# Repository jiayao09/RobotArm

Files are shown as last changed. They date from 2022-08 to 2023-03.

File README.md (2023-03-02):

# RobotArm
This a robotic arm with a 4 DOF developed based on MeArm model for further development. Take a look at my BOM and assembly drawing PDF to build the same model.
(check out start.ino)


Figure 1:Robotic arm with Laser cutting update
</br>
</br>

https://user-images.githubusercontent.com/110358483/185725085-09091f4c-c75e-4899-8eab-52e4dab4b233.mp4

# list of file
- Detail BOM
- STL file for 3D printing
- Laser cutting file for gripper version 2 (optional)
- Assembly drawings for installation
- Code for the above video （Control Board：Arduino）

</br>

#  RECENT UPDATE:
I've recently decided to increase the arm's degrees of freedom from 4 to 6. This design demo builds upon the Niryo One concept by adding new elements. The detail drawing and bill of materials (BOM) is up-to-date. The new design expands on the original functionality by including new interfaces and hardware.



### Check out the development process here:  https://github.com/jiayao09/RobotArm/tree/6-DOF-Robot-Arm

</br>

# Included Functions:
### Control by coding

https://user-images.githubusercontent.com/110358483/185726008-0d00c303-87b9-40a1-b045-875e55abf965.mp4

### Control by phone with the HC-06 Bluetooth module (check out start.ino)

https://user-images.githubusercontent.com/110358483/185725174-6e9ee21b-cd90-49b7-b49f-77a15e82c952.mp4

</br>

### Control by Wearable-Controller
Check out more information here: https://github.com/jiayao09/Wearable_Controller.git
- Sensor and control board:
   - Arduino uno
   - Servo KN99 X 4
   - NRF24L01



</br>

### Control by ESP32 cam for image recognition (Pending)
- Add object or color detection
- Move to detect object position

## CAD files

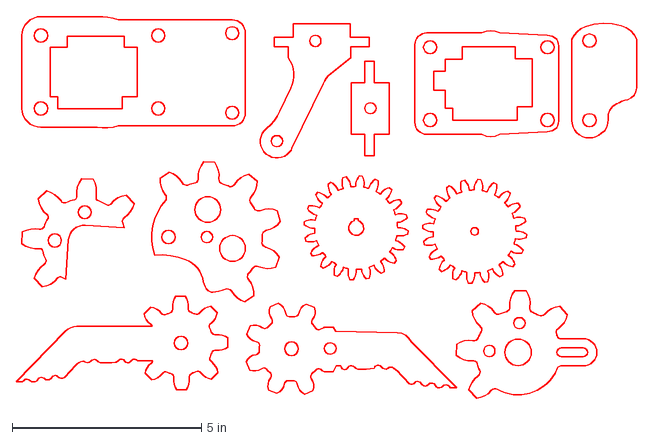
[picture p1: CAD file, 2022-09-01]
3mm.dxf
16.4 x 10.2 in

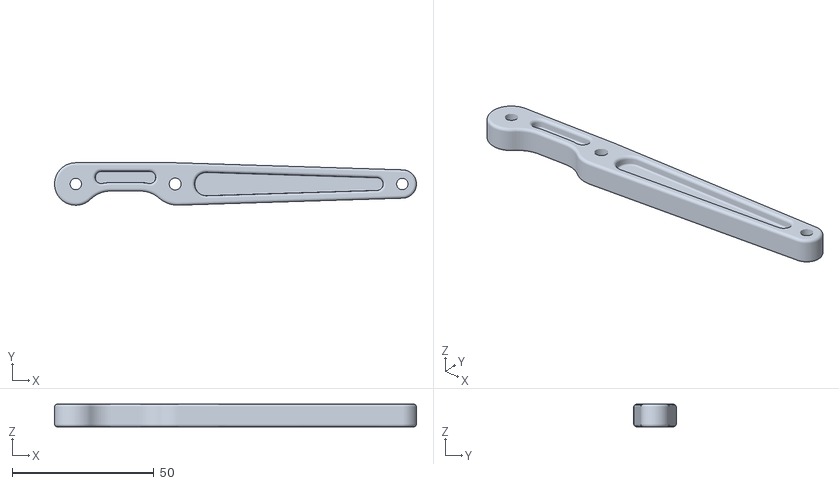
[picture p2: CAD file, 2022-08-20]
STL file/EBA_01.00.005_horizontal_arm.STL
127.5 x 15.0 x 8.00

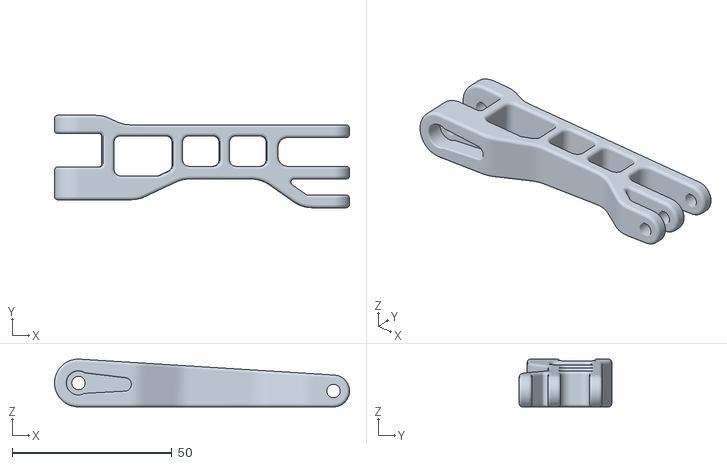
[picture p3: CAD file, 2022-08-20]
STL file/EBA_01.00.004_forward_drive_arm.STL
92.5 x 29.0 x 15.0

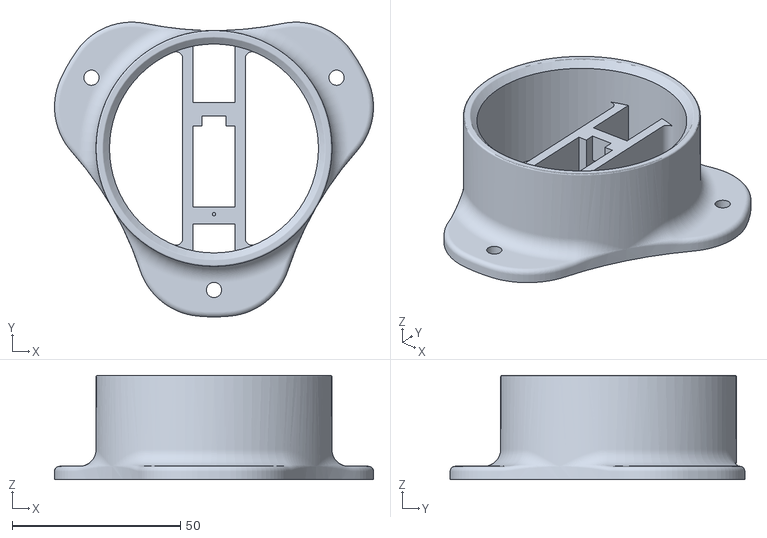
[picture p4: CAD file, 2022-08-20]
STL file/EBA_01.00.010_basement.STL
94.7 x 87.5 x 31.0

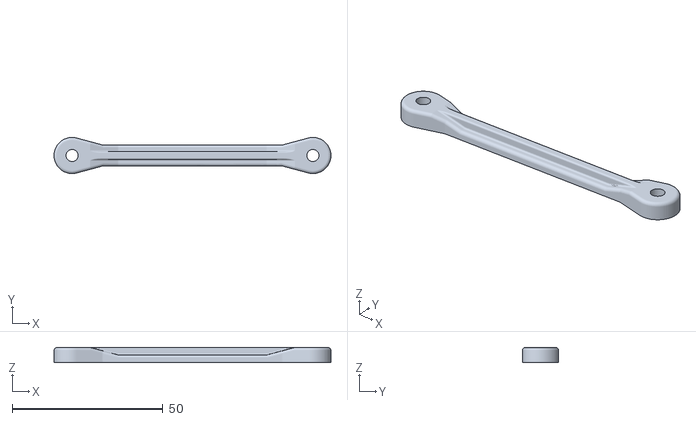
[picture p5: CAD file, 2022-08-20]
STL file/EBA_01.00.003_link.STL
92.0 x 12.0 x 5.00

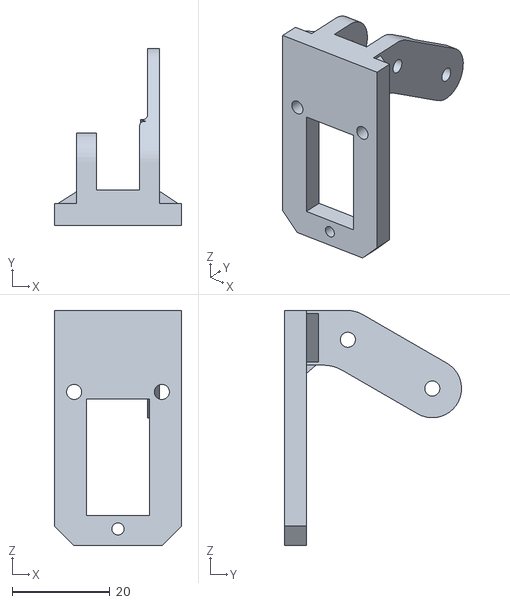
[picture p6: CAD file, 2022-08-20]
STL file/EBA_01.00.012_R01_claw_support_upgrade.STL
26.1 x 36.3 x 48.2

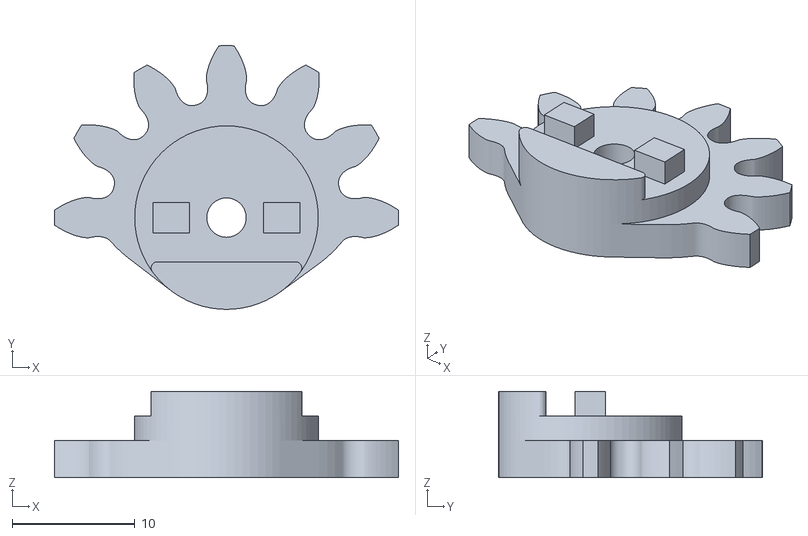
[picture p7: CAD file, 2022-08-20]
STL file/EBA_01.00.016_R01_driven_gear.STL
28.0 x 21.5 x 7.00

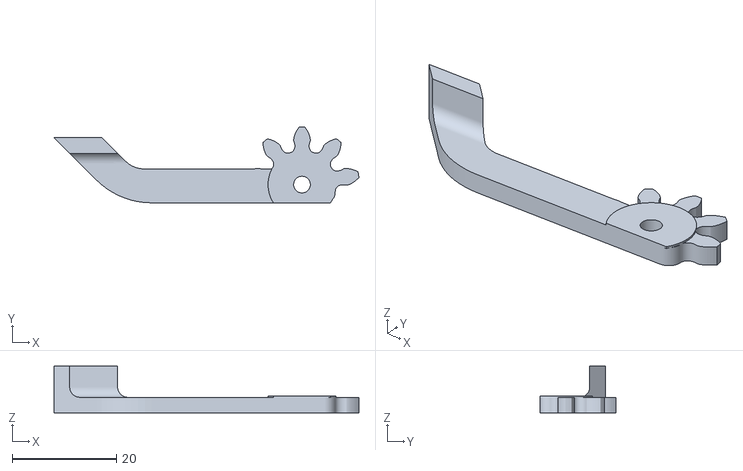
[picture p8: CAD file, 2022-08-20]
STL file/EBA_01.00.014_R01_left_finger.STL
58.4 x 14.5 x 9.00

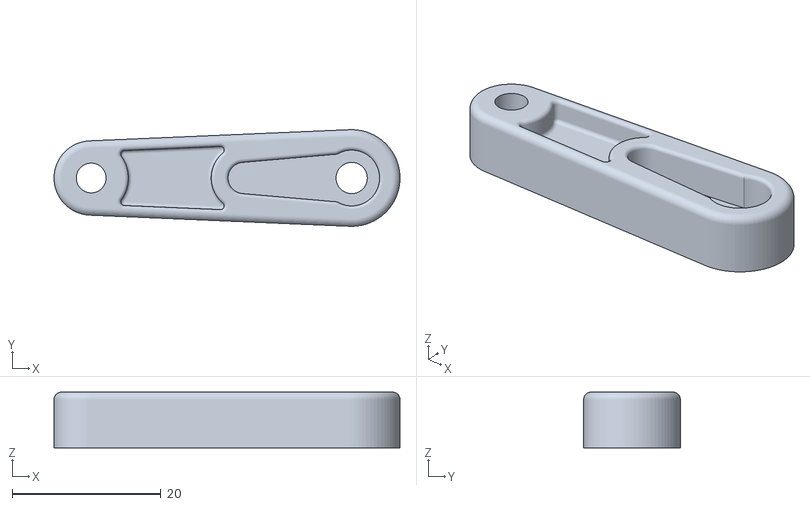
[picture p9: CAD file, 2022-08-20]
STL file/EBA_01.00.002_vertical_drive_arm.STL
46.5 x 13.0 x 7.50

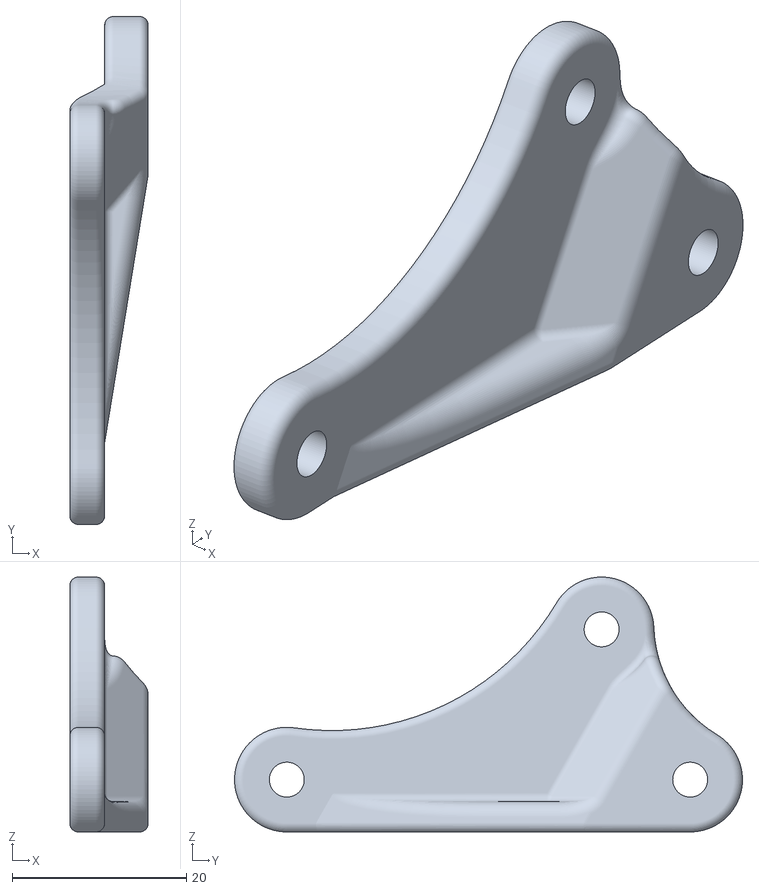
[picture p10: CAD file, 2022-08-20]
STL file/EBA_01.00.006_triangular_link.STL
9.00 x 58.3 x 29.2

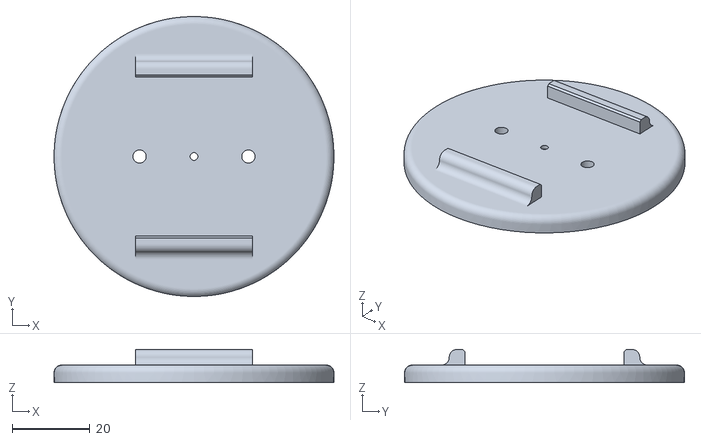
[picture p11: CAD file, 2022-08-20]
STL file/EBA_01.00.011_round_plate.STL
72.0 x 72.0 x 8.50

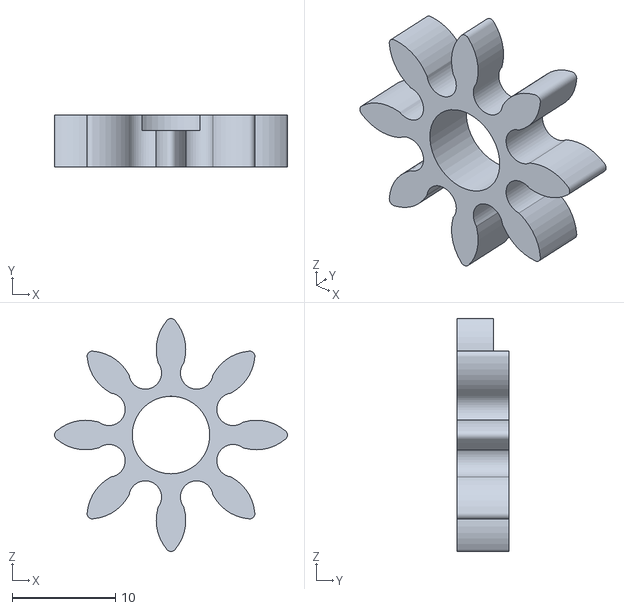
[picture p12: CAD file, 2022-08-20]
STL file/EBA_01.00.015_drive gear_upgrade.STL
22.5 x 5.00 x 22.5

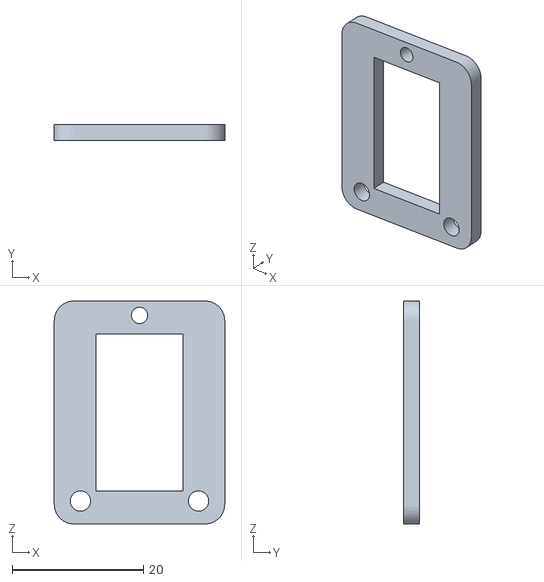
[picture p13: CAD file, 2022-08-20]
STL file/EBA_01.00.009_servo_plate_upgrade.STL
26.0 x 2.50 x 34.0

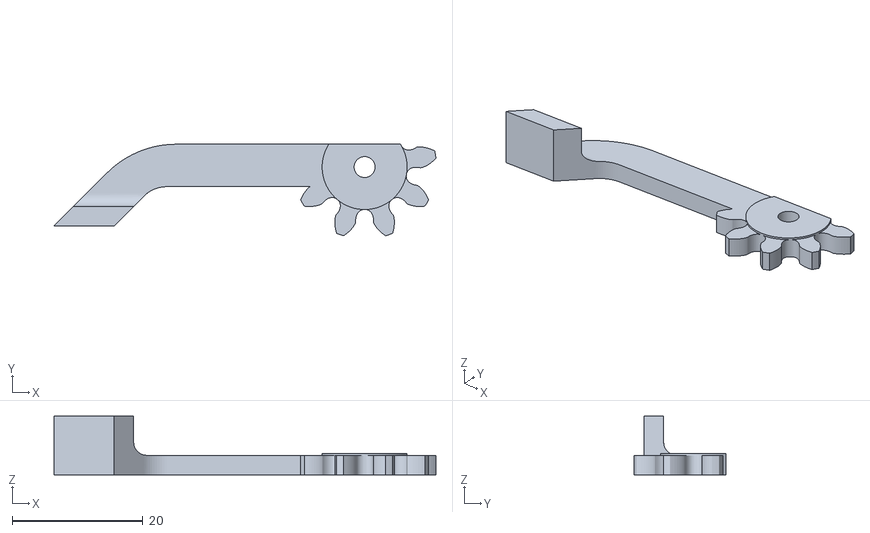
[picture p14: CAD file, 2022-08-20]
STL file/EBA_01.00.013_R01_right_finger.STL
58.4 x 14.0 x 9.00

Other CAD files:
STL file/EBA_01.00.001.STL

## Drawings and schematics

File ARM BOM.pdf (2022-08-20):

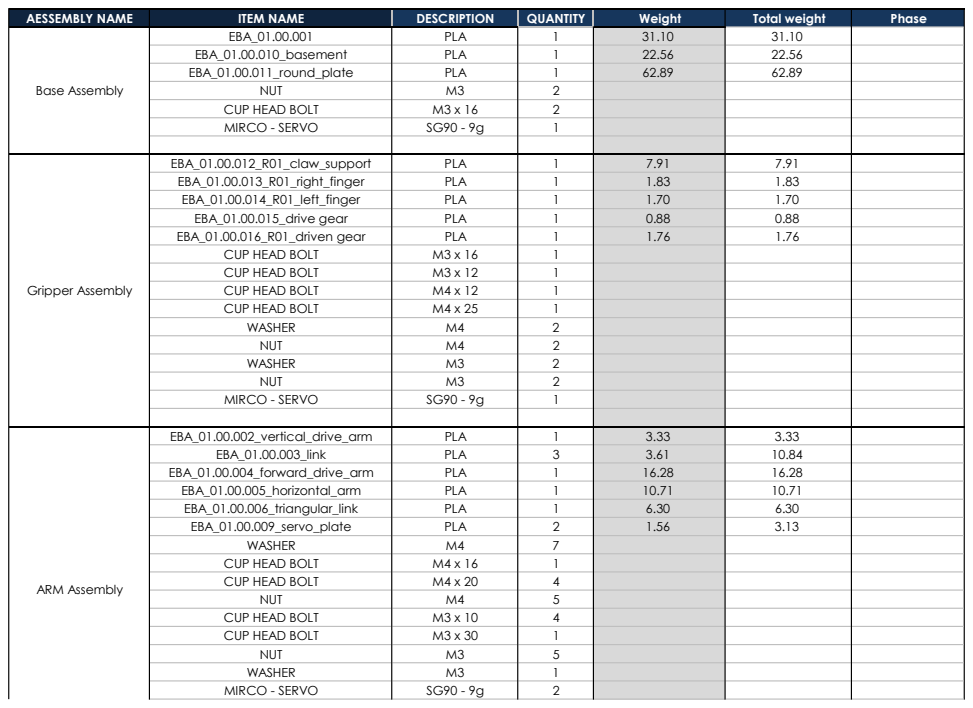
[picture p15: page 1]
EBA_01.00.012_R01_claw_support; PLA; EBA_01.00.013_R01_right_finger; EBA_01.00.014_R01_left_finger; EBA_01.00.015_drive gear; EBA_01.00.016_R01_driven gear; CUP HEAD BOLT; WASHER; NUT; MIRCO - SERVO; EBA_01.00.002_vertical_drive_arm; EBA_01.00.003_link; EBA_01.00.004_forward_drive_arm; EBA_01.00.005_horizontal_arm; EBA_01.00.006_triangular_link; EBA_01.00.009_servo_plate; Gripper Assembly; ARM Assembly

AESSEMBLY NAME | ITEM NAME | DESCRIPTION | QUANTITY | Weight | Total weight 31.10 22.56 62.89 | Phase
Base Assembly | EBA_01.00.001 EBA_01.00.010_basement EBA_01.00.011_round_plate NUT CUP HEAD BOLT MIRCO - SERVO | PLA PLA PLA M3 M3 x 16 SG90 - 9g | 1 1 1 2 2 1 | 31.10 22.56 62.89

Tube 1 | 4 x 3 x 22 | 1
Tube 2 | 4 x 3 x 26 | 1
Total weight | 181.21
Est Cost($0.08/g) | 14.50
Actual Cost | 11.28

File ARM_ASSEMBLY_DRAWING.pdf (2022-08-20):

E E

F F

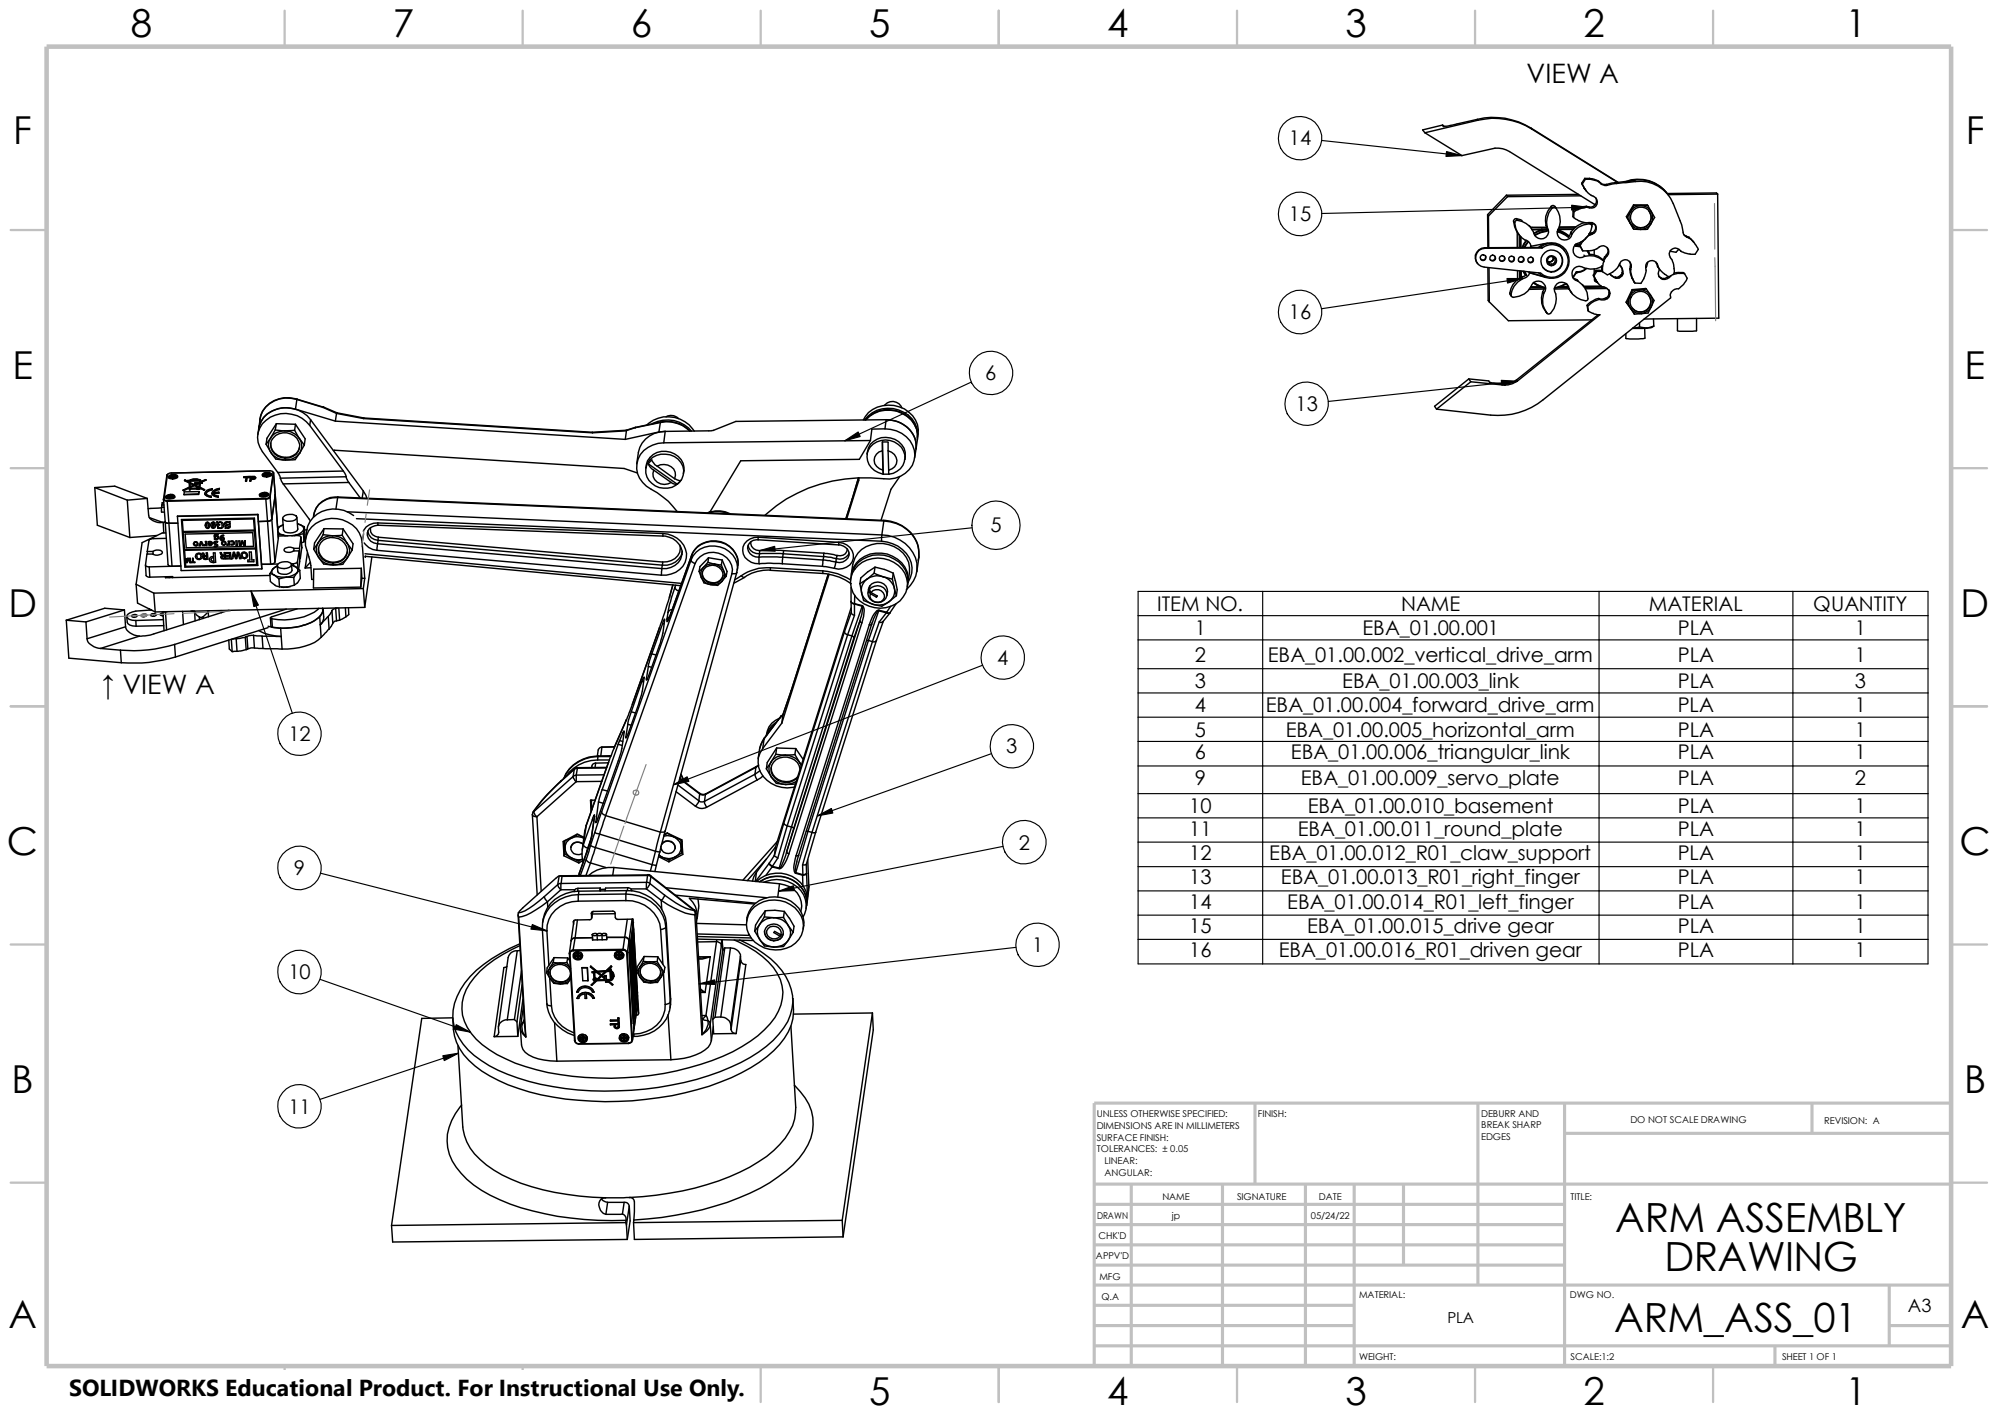
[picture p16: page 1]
SHEET 1 OF 1; WEIGHT:; BREAK SHARP; DO NOT SCALE DRAWING; REVISION: A; FINISH:; EDGES; SCALE:1:2; DEBURR AND; ↑ VIEW A; VIEW A

ITEM NO. | NAME | MATERIAL | QUANTITY
1 | EBA_01.00.001 | PLA | 1
2 | EBA_01.00.002_vertical_drive_arm | PLA | 1
3 | EBA_01.00.003_link | PLA | 3
4 | EBA_01.00.004_forward_drive_arm | PLA | 1
5 | EBA_01.00.005_horizontal_arm | PLA | 1
6 | EBA_01.00.006_triangular_link | PLA | 1
9 | EBA_01.00.009_servo_plate | PLA | 2
10 | EBA_01.00.010_basement | PLA | 1
11 | EBA_01.00.011_round_plate | PLA | 1
12 | EBA_01.00.012_R01_claw_support | PLA | 1
13 | EBA_01.00.013_R01_right_finger | PLA | 1
14 | EBA_01.00.014_R01_left_finger | PLA | 1
15 | EBA_01.00.015_drive gear | PLA | 1
16 | EBA_01.00.016_R01_driven gear | PLA | 1

UNLESS OTHERWISE SPECIFIED:
DIMENSIONS ARE IN MILLIMETERS
SURFACE FINISH:
TOLERANCES: ± 0.05
LINEAR:
ANGULAR:

NAME | SIGNATURE | DATE | | | | TITLE: ARM ASSEMBLY DRAWING

DRAWN | jp | | 05/24/22

CHK'D
APPV'D
Q.A | | | | MATERIAL: PLA | DWG NO. ARM_ASS_01 | A3

MFG

SOLIDWORKS Educational Product. For Instructional Use Only.

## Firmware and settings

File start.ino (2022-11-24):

#include <Servo.h>
void armDataCmd(char serialCmd);
void reportStatus();
void armIniPos();
void action();
void armJoyCmd(char serialCmd);
int checkStatus(int servoData, int maxInput, int minInput);
void servoCmd(char serialName, int servoData, int Delay);
Servo base, fArm, rArm, claw;

int basePos = 90;
int rArmPos = 90;
int fArmPos = 90;
int clawPos = 50;

int DSD = 15;  // Defailt Servo Delay

const int baseMin = 30;
const int baseMax = 150;
const int rArmMin = 45;
const int rArmMax = 130;
const int fArmMin = 45;
const int fArmMax = 150;
const int clawMin = 0;
const int clawMax = 50;

bool mode; // mode = 1: command contorl, mode = 0: keyboard control
int moveStep = 3;

void setup() {
  base.attach(11);     // base 
  delay(200);
  rArm.attach(10);     // rArm 
  delay(200);
  fArm.attach(9);      // fArm 
  delay(200);
  claw.attach(6);      // claw 
  delay(200);
  
  base.write(basePos);
  delay(10);
  fArm.write(fArmPos);
  delay(10);
  rArm.write(rArmPos);
  delay(10);
  claw.write(clawPos);
  delay(10);
  
  Serial.begin(9600);
  Serial.println("Input control signal");
}

void loop() {
  if (Serial.available()>0){
    char serialCmd = Serial.read();
    if(mode == 1){
      armDataCmd(serialCmd);
    } else{
      armJoyCmd(serialCmd);
    }
  }
}

void armDataCmd(char serialCmd){
  Serial.print("Serial commod = ");
  Serial.print(serialCmd); 
  Serial.print("     "); 
  if (serialCmd == 'b' || serialCmd == 'c' || serialCmd == 'f' || serialCmd == 'r'){
      int servoData = Serial.parseInt();
      servoCmd(serialCmd, servoData, DSD);
  } else {
  switch(serialCmd){
    case 'o':
      reportStatus();
      break;
    case 'i':
      armIniPos();
      break;
    case 'a':
        action();
        break;
    case 'm':
      mode = 0;
      Serial.println("Command: Switch mode");
      break;   
    default:
      Serial.println("Unknown Command");
    }
  }
}

void armJoyCmd(char serialCmd){
  int baseJoyPos;
  int rArmJoyPos;
  int fArmJoyPos;
  int clawJoyPos;
  switch(serialCmd){
    case 'a':
      baseJoyPos = base.read() - moveStep;
      servoCmd('b', baseJoyPos, DSD);
      break;
    case 'd':
      baseJoyPos = base.read() + moveStep;
      servoCmd('b', baseJoyPos, DSD);
      break;
    case 'w':
      rArmJoyPos = rArm.read() + moveStep;
      servoCmd('r', rArmJoyPos, DSD);
      break;
    case 's':
      rArmJoyPos = rArm.read() - moveStep;
      servoCmd('r', rArmJoyPos, DSD);
      break;
    case 'e':
      fArmJoyPos = fArm.read() + moveStep;
      servoCmd('f', fArmJoyPos, DSD);
      break;
    case 'f':
      fArmJoyPos = fArm.read() - moveStep;
      servoCmd('f', fArmJoyPos, DSD);
      break;
    case 'r':
      clawJoyPos = claw.read() + moveStep;
      servoCmd('c', clawJoyPos, DSD);
      break;
    case 't':
      clawJoyPos = claw.read() - moveStep;
      servoCmd('c', clawJoyPos, DSD);
      break;
    case 'm':
      mode = 1;
      Serial.println("Command: Switch mode");
      break;
    case 'o':
      servoCmd('b', basePos, DSD);
      servoCmd('r', fArmPos, DSD);
      servoCmd('f', rArmPos, DSD);
      servoCmd('c', 0, DSD);     
    case 'i':
      armIniPos();
      break;      
    default:
      Serial.println("Unknown Command");
  }
}
    
void action(){
  armIniPos();
  delay(2000);
  int robotactionArray[4][3] = {
    {'c',0,DSD},
    {'b',120,DSD},
    {'f',120,DSD},
    {'r',45,DSD},
  };
  for(int i = 0; i < 4; i++){
    servoCmd(robotactionArray[i][0], robotactionArray[i][1], robotactionArray[i][2]);
    delay(200);
  }
}
  
void armIniPos(){
  servoCmd('b', basePos, DSD);
  servoCmd('r', fArmPos, DSD);
  servoCmd('f', rArmPos, DSD);
  servoCmd('c', clawPos, DSD);
}

void reportStatus(){
  Serial.println("++++++++++ Robot-Arm Status Report +++++");
  Serial.print("Claw Postition: clawPos = "); Serial.println(claw.read());
  Serial.print("Base Position: basePos = "); Serial.println(base.read());
  Serial.print("Rear Arm Position : rArmPos = "); Serial.println(rArm.read());
  Serial.print("Front Arm Position : fArmPos = "); Serial.println(fArm.read());  
  Serial.println("++++++++++++++++++++++++++++++++++++++++");
}

int checkStatus(int servoData, int maxInput, int minInput){
  int servo = 0;
  if (servoData >= minInput && servoData <= maxInput) {
    servo = servoData;
  } else if (servoData < minInput) {
    servo = minInput;
    Serial.println(" "); Serial.print("Warning: Servo Value is out of Limit!");
    Serial.print("Choose range between "); Serial.print(minInput);Serial.print(" and ");Serial.println(maxInput);
  }
  else {
    servo = maxInput;
    Serial.print("Warning: Servo Value is out of Limit! ");
    Serial.print("Choose range between "); Serial.print(minInput);Serial.print(" and ");Serial.println(maxInput);
  }
  Serial.print("Target angle = "); 
  Serial.println(servo); 
  return(servo);
}


void servoCmd(char serialName, int servoData, int Delay){
  Servo servo2go;
  int fromPos;
  int toPos;
  switch(serialName){
    case 'b':
      servo2go = base;
      fromPos = base.read();
      toPos = checkStatus(servoData, baseMax, baseMin);
      break;
    case 'r':
      servo2go = rArm;
      fromPos = rArm.read();
      toPos = checkStatus(servoData, rArmMax, rArmMin);
      break;
    case 'f':
      servo2go = fArm;
      fromPos = fArm.read();
      toPos = checkStatus(servoData, fArmMax, fArmMin);
      break;
    case 'c':
      servo2go = claw;
      fromPos = claw.read();
      toPos = checkStatus(servoData, clawMax, clawMin);
      Delay = 1;
      break;
  }
  
  if (fromPos <= toPos){
    for(int i = fromPos; i<= toPos; i++){
      servo2go.write(i);
      delay(Delay);
    } 
  }  else {
      for(int i = fromPos; i >= toPos; i--){
      servo2go.write(i);
      delay(Delay);
      }
  }
}
